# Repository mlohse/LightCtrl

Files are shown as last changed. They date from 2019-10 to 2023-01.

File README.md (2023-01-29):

# LightCtrl

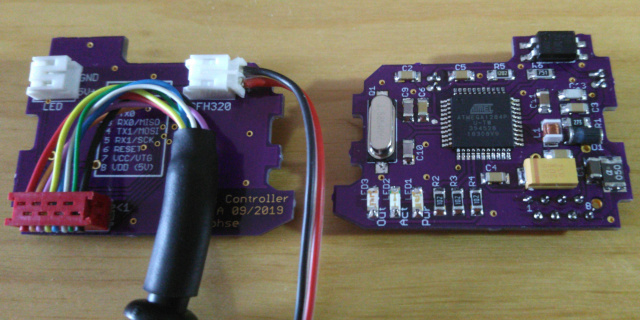
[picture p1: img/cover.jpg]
cover image


Light Controller for Egret TenV4 electric scooter

The goal of this project is to power the scooter's front light from the main LiPo battery instead of using 4x throw-away alkaline batteries (AAA).
Further, it allows the light to be switched on/off conveniently via the throttle controller's power button (same as the rear light)
or have the light switched on/off automatically when it's getting dark (e.g. in tunnels or at night).

The PCB needs to be installed into the front light's battery compartment. The on/off switch is no longer needed and can be replaced by a photo transistor.

A short demo video (German) is available on vimeo: https://vimeo.com/364582430

# Required Skills
Before you consider building your own, please be aware that you'll need some skills here:

* You should be able to solder SMD! I've chosen large components (1206) for the PCB, but of course there is the 44-pin package of the ATMEGA, which may need some practice and a decent solder iron/station.

* The PCB and front light is powered via the 5V USB supply of the scooters throttle controller and needs to be connected in series to the throttle controller's tx data line (white cable).
  This can be accomplished by either opening/modifying the throttle controller (see instructions below) or creating an adapter cable which can be installed between the throttle and the motor controller (in the battery compartment).

* The front light's plastic case needs some mechanical modification to fit a cable through the housing (drill a hole) and fit PCB into the battery compartment.

* You'll need to remove the front light's on/off switch and solder wire between the voltage regulators enable pin (again SMD) and ground, see description below...

* You'll need an ISP-programmer for flashing the firmware (those are available on Ebay for ~15 Euro)

This project is certainly not suitable for beginners and of course I won't take any liability if you break your scooter or any components of it.

# Bill of Material (BOM)
The PCB can be ordered at OSH Park (they ship worldwide):

* https://oshpark.com/shared_projects/gwnaN0r6 (rev.B)

It doesn't really matter of which brand/type you order resistors and capacitors, nor does this board require any tight tolerances. You can purchase whatever your local hardware dealer has on stock fitting the value/package described by the schematic.
However, for convenience I've created a virtual shopping basket at Reichelt Elektronik:

* https://www.reichelt.de/my/1627216

Unfortunately, the AQY212EH isn't available at Reichelt, but you can order it from Buerklin,
Order-No.: 29G8736

* https://www.buerklin.com/de/Produkte/Elektromechanik/Relais-und-Sch%C3%BCtze/PhotoMOS-Relais/AQY-212-EHA%2C-SMD-Relais/p/29G8736

Further, I've tried several (low-cost) usb cables from Amazon which didn't quite fit my needs, until I came across these 2:

* https://www.amazon.de/gp/product/B01I1HXRK8/ (this is actually much shorter than 40cm, I measured only 34cm!)

* https://www.amazon.de/gp/product/B00P0ES0VC/

The UGreen USB3 extension cable is of decent quality and can be crimped perfectly into the Micromatch connector.
(Yes, it needs to be cut into halves: The female connector is needed for the front light, the male can be used to build an adapter for the ISP programmer)

# Building and Flashing the Firmware
You need to have an AVR toolchain installed (make, gcc, binutils)

On Arch Linux simply install the following packages:

`# pacman -S community/avr-gcc community/avr-binutils community/avr-libc`

I'm still using my good old AVR Dragon (unfortunately, it seems to be out of production), which needs to have avrdude installed:

`# pacman -S avrdude`

If you own a different programmer there is a good chance it's also supported by avrdude, otherwise just install whatever software it needs and don't forget to adopt the programmer/fuses section of the Makefile accordingly.

To build the firmware change into the `src` directory and run:

`# make`

...then connect the board to your ISP programmer (it needs to be powered through the programmer!) and flash the fuses:

`# make fuses`

...and firmware:

`# make program`

Done.

# Front Light PCB Modification
1. Remove the on/off switch and undervoltage indicator led (no longer needed)
2. Connect the voltage regulator's enable pin (outer pin) to GND, as shown:
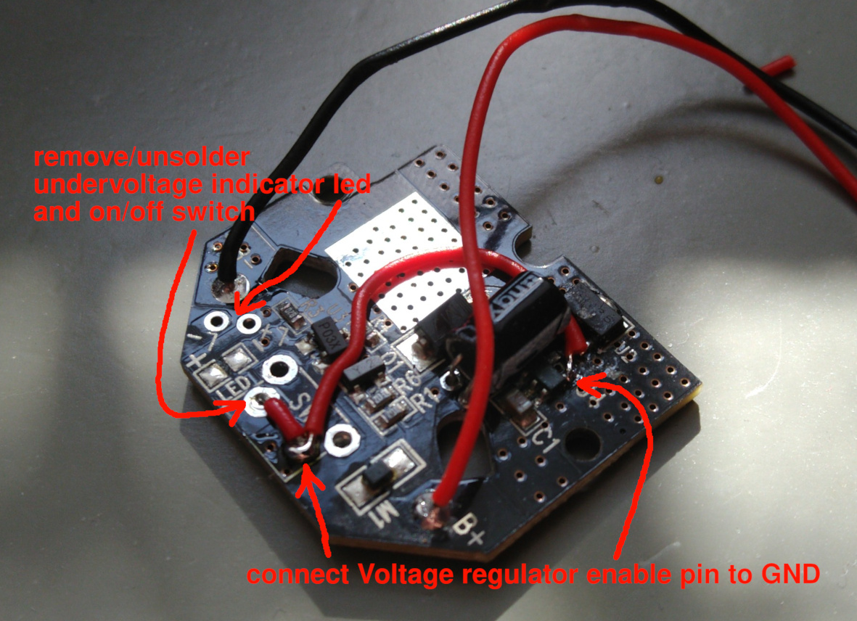
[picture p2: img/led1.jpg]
front light pcb modification


# Throttle Controller Modification
1. Open the throttle controller (it is glued with silicone and requieres some force - use a knife or sharp piece of metal). Once open remove the USB socket which is also glued in with silicone and clean it as best as you can:
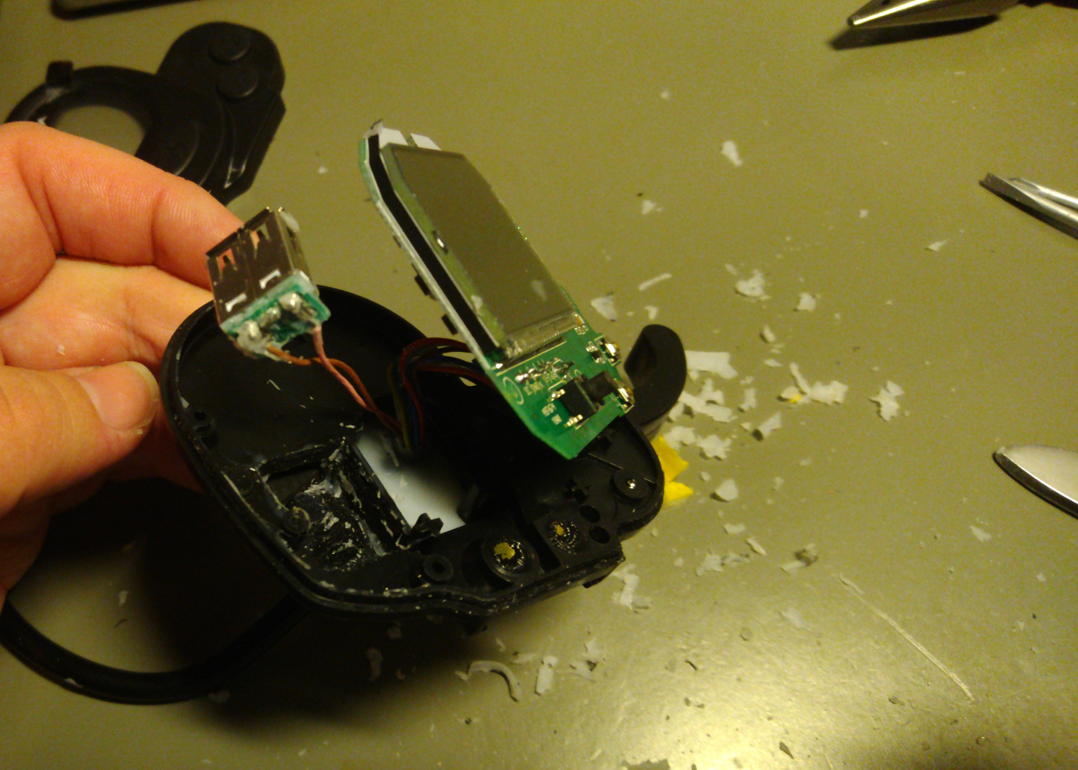
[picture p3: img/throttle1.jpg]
open throttle controller


2. Unsolder the TX data wire (white, labels as T6):
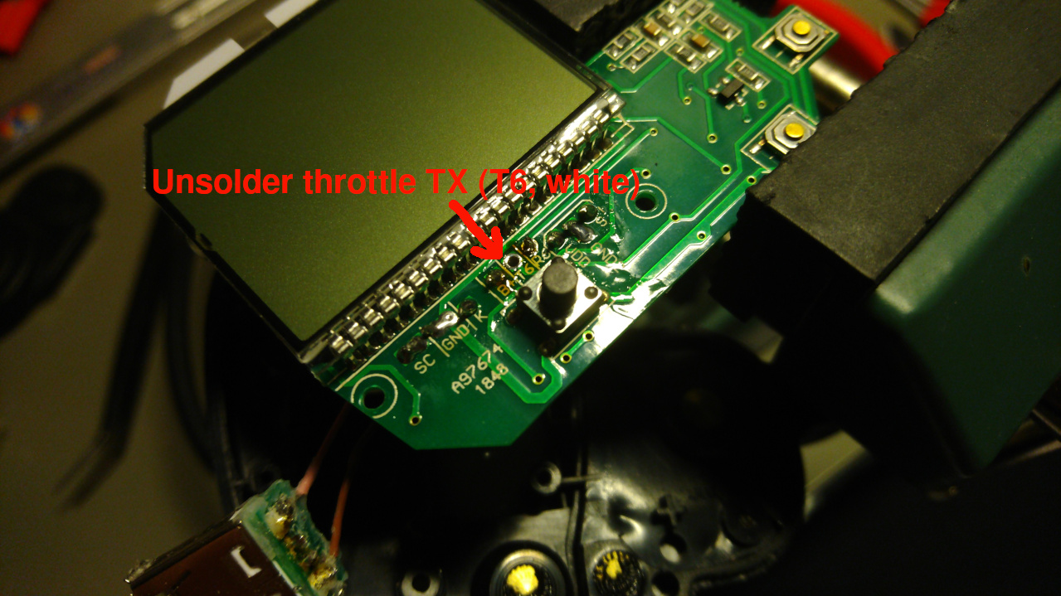
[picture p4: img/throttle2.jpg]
tx data wire


3. Open the solder bridge between the USB data lines:
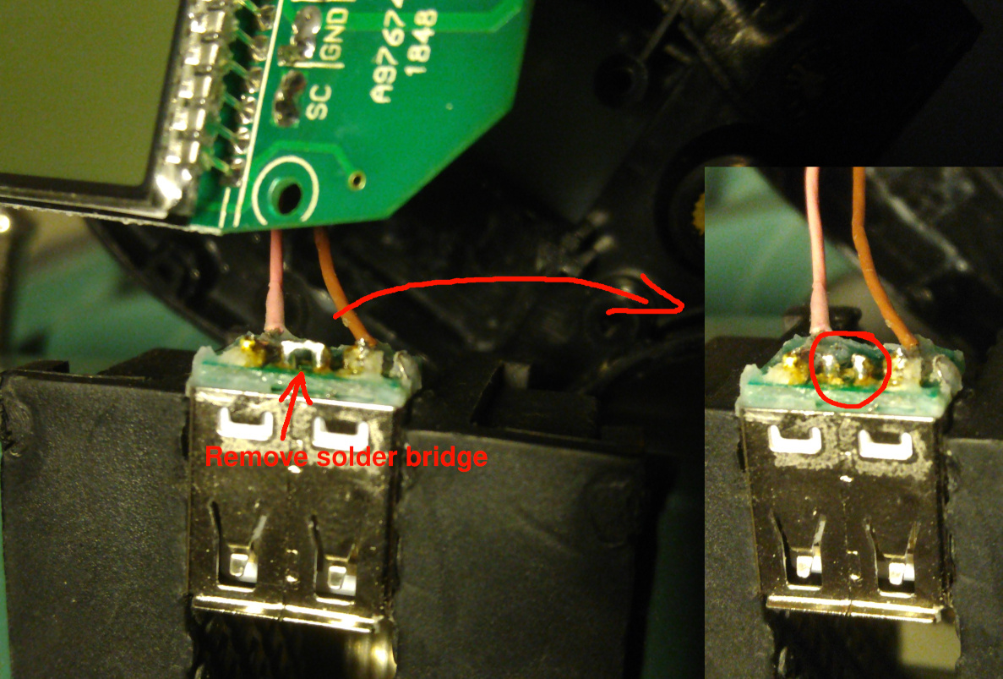
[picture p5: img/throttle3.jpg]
usb solder bridge


4. Conntect the white cabel (which was soldered to throttle T6 previously) to the USB data line and add a new cable from the other usb data line to the throttle's T6 pin. Note: the 4k7 resistor is optional. If it is installed the scooter can be started without the LightCtrl pcb connected. If it is not fitted, the throttle will show an error if powered on without it. This may be usefull as a weak theft-protection (if you take the front-light with you when you leave the scooter alone).
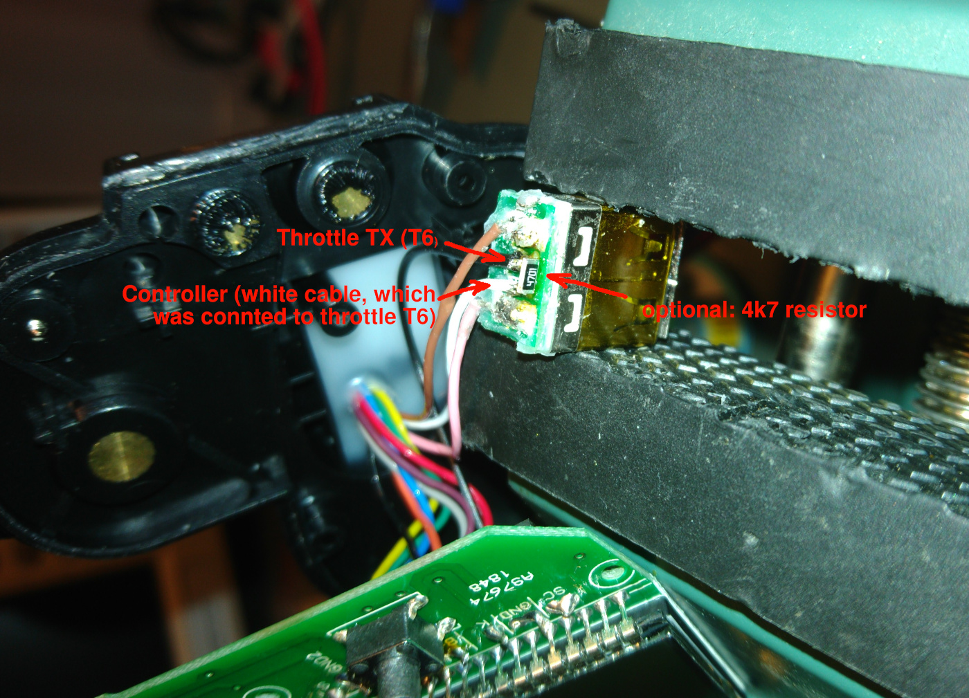
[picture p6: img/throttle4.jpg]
usb data lines connected


5. Use some hot glue to put the USB socket back in
Important: After modification the USB socket can no longer be used to charge usb devices! Do not plug in your cell phone!

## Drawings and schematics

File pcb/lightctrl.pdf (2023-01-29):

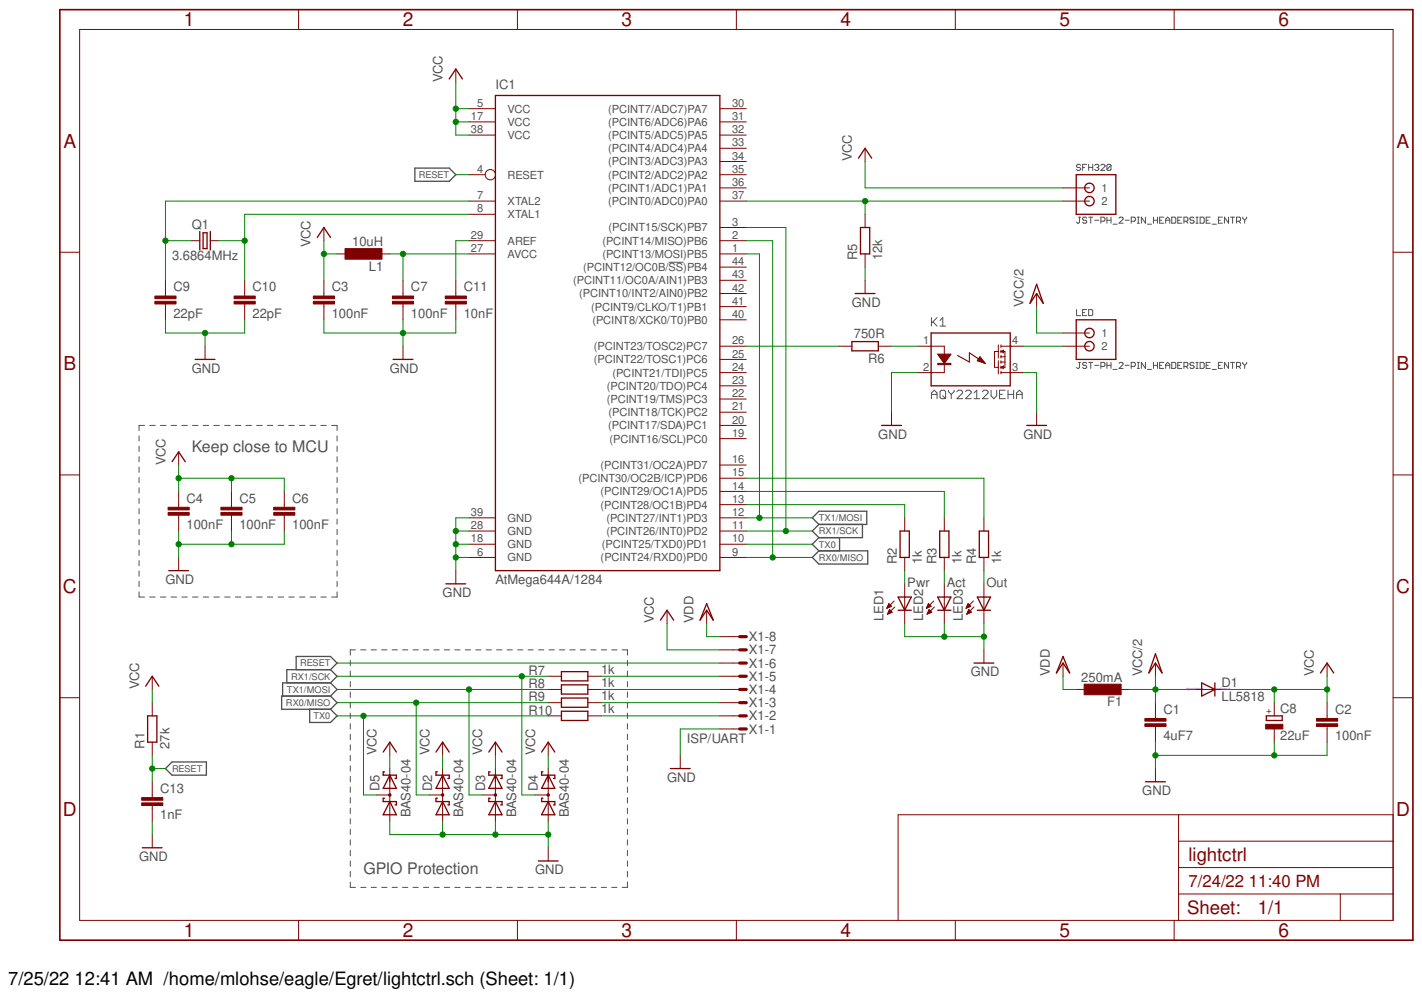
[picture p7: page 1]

VCC
Keep close to MCU

7/25/22 12:41 AM /home/mlohse/eagle/Egret/lightctrl.sch (Sheet: 1/1)

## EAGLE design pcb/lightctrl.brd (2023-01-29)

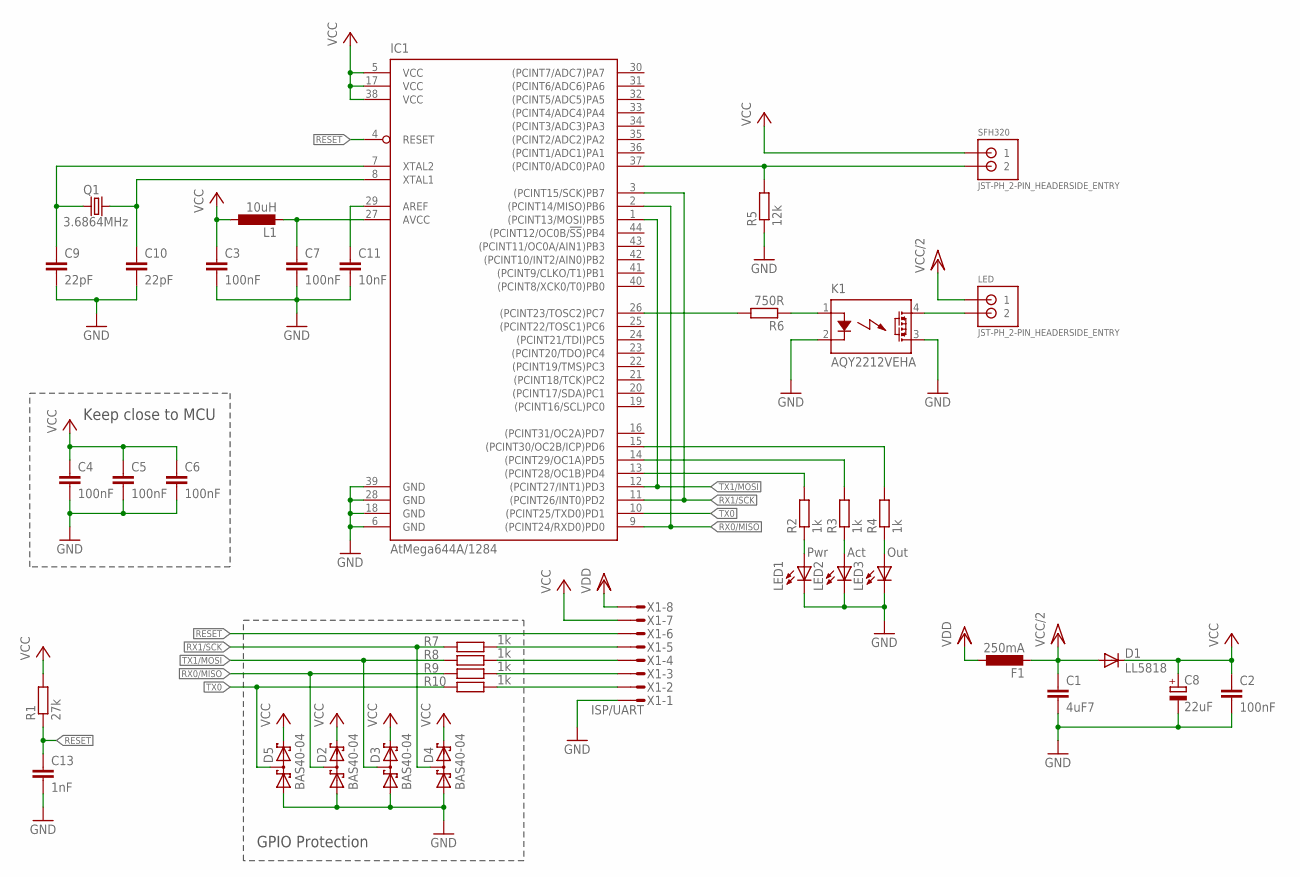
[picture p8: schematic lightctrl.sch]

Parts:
C1: 4uF7; C1206
C2, C3, C4, C5, C6, C7: 100nF; C1206
C8: 22uF; SMC_D
C9, C10: 22pF; C1206
C11: 10nF; C1206
C13: 1nF; C1206
D1: LL5818; MELF-MLL41
D2, D3, D4, D5: BAS40-04; SOT23
F1: 250mA; L1812
IC1: AtMega644A/1284; TQFP44
K1: AQY2212VEHA; SMD-DIP04
L1: 10uH; L3230M
LED: JST-PH_2-PIN_HEADERSIDE_ENTRY; S2B-PH_HEADER
LED1: Pwr; CHIPLED_1206
LED2: Act; CHIPLED_1206
LED3: Out; CHIPLED_1206
Q1: 3.6864MHz; HC49UP
R1: 27k; R1206
R2, R3, R4, R7, R8, R9, R10: 1k; R1206
R5: 12k; R1206
R6: 750R; R1206
SFH320: JST-PH_2-PIN_HEADERSIDE_ENTRY; S2B-PH_HEADER
X1: ISP/UART; MICROMATCH-8

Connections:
GND: C1.2, C2.2, C3.2, C4.2, C5.2, C6.2, C7.2, C8.-, C9.2, C10.2, C11.2, C13.2, D2.1 (A1), D3.1 (A1), D4.1 (A1), D5.1 (A1), IC1.6 (GND), IC1.18 (GND), IC1.28 (GND), IC1.39 (GND), K1.2 (K), K1.3 (DS2), LED1.C, LED2.C, LED3.C, R5.1, X1.1
unnamed: C7.1, IC1.27 (AVCC), L1.2
unnamed: IC1.37 ((PCINT0/ADC0)PA0), R5.2, SFH320.P2 (2)
unnamed: C11.1, IC1.29 (AREF)
unnamed: C10.1, IC1.8 (XTAL1), Q1.2
unnamed: C9.1, IC1.7 (XTAL2), Q1.1
unnamed: K1.4 (DS1), LED.P2 (2)
unnamed: LED1.A, R2.1
unnamed: LED2.A, R3.1
unnamed: LED3.A, R4.1
unnamed: IC1.13 ((PCINT28/OC1B)PD4), R2.2
unnamed: IC1.14 ((PCINT29/OC1A)PD5), R3.2
unnamed: IC1.15 ((PCINT30/OC2B/ICP)PD6), R4.2
unnamed: R7.2, X1.5
unnamed: K1.1 (A), R6.1
unnamed: R8.2, X1.4
unnamed: R9.2, X1.3
unnamed: IC1.26 ((PCINT23/TOSC2)PC7), R6.2
unnamed: R10.2, X1.2
RESET: C13.1, IC1.4 (RESET), R1.1, X1.6
RX0/MISO: D2.3 (C1A2), IC1.2 ((PCINT14/MISO)PB6), IC1.9 ((PCINT24/RXD0)PD0), R9.1
RX1/SCK: D4.3 (C1A2), IC1.3 ((PCINT15/SCK)PB7), IC1.11 ((PCINT26/INT0)PD2), R7.1
TX0: D5.3 (C1A2), IC1.10 ((PCINT25/TXD0)PD1), R10.1
TX1/MOSI: D3.3 (C1A2), IC1.1 ((PCINT13/MOSI)PB5), IC1.12 ((PCINT27/INT1)PD3), R8.1
VCC: C2.1, C3.1, C4.1, C5.1, C6.1, C8.+, D1.C, D2.2 (C2), D3.2 (C2), D4.2 (C2), D5.2 (C2), IC1.5 (VCC), IC1.17 (VCC), IC1.38 (VCC), L1.1, R1.2, SFH320.P1 (1), X1.7
VCC/2: C1.1, D1.A, F1.2, LED.P1 (1)
VDD: F1.1, X1.8

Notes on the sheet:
GPIO Protection
Keep close to MCU

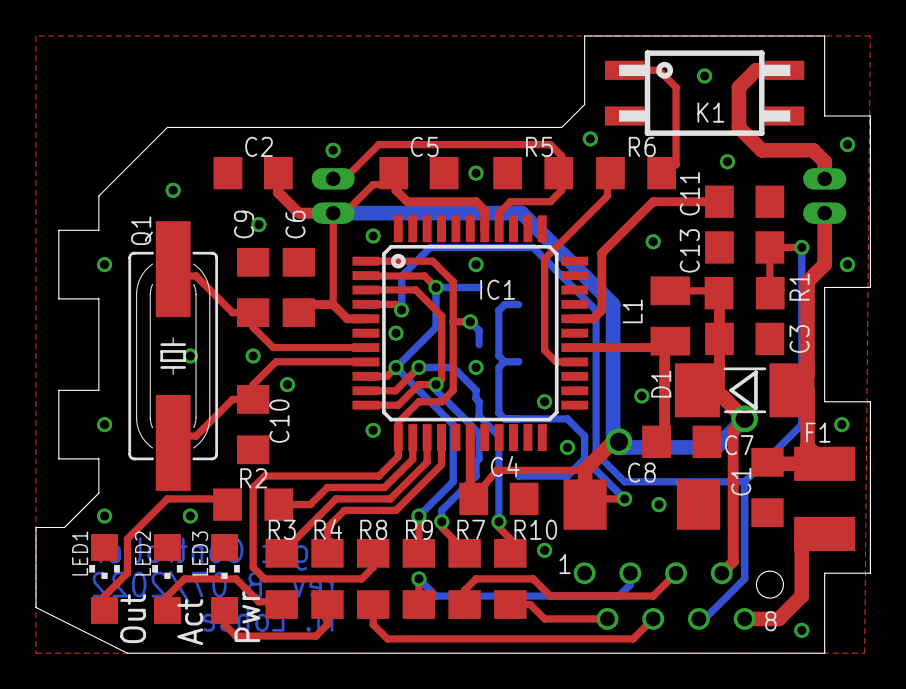
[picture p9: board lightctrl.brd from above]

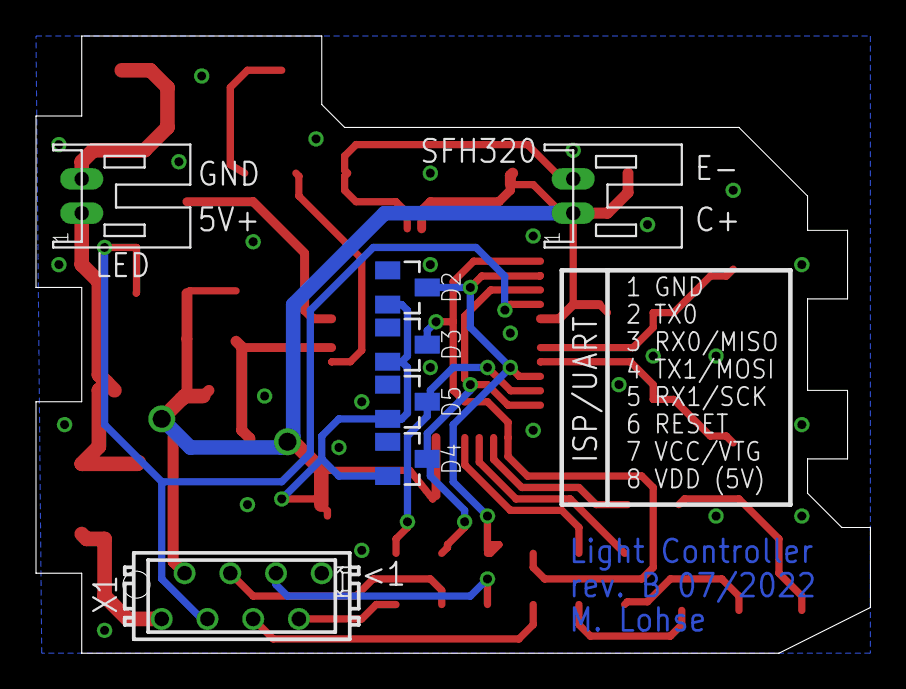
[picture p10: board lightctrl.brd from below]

Board: 2 copper layers, 46.4 x 34.3 mm, 38 parts (7 on the bottom side), 27 nets.

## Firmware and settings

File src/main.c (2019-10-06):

/*******************************************************************************
 * main.c                                                                      *
 * author:  Markus Lohse <mlohse@gmx.net>                                      *
 * date:    2019-09-24                                                         *
 * license: LGPLv3, see https://www.gnu.org/licenses/lgpl-3.0.txt              *
 ******************************************************************************/
#include <avr/io.h>
#include "adc.h"
#include "led.h"
#include "uart.h"
#include "config.h"
#include "ctrl.h"
#include "timer.h"


static void init(void)
{
	/* configure & initialize io ports */
	DDRA = IO_DDRA;
	DDRB = IO_DDRB;
	DDRC = IO_DDRC;
	DDRD = IO_DDRD;
	
	PORTA = INIT_PORTA;
	PORTB = INIT_PORTB;
	PORTC = INIT_PORTC;
	PORTD = INIT_PORTD;

	timer_init();
	uart_init();
	led_flash();
	uart0_flush();
	adc_init();
}

int main(void)
{
	init();
	adc_start();

	while(1)
	{
		ctrl_run();
		led_set(LED_PWR, (timer_uptime() % 2000) < 1000);
	}
}

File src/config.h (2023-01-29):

/*******************************************************************************
 * Config file for Egret Light Controller board rev. A                         *
 * author:  Markus Lohse <mlohse@gmx.net>                                      *
 * date:    2019-09-24                                                         *
 * license: LGPLv3, see https://www.gnu.org/licenses/lgpl-3.0.txt              *
 ******************************************************************************/
#ifndef CONFIG_H_
#define CONFIG_H_

/***********************************
 * IO Ports                        *
 ***********************************/
#define IO_DDRA                 0xFE    // PortA [1..7] unused out, 0 sensor input
#define IO_DDRB                 0x1F    // PortB [0..4] unused out, 5 mosi/tx1 -> PD3 in, 6 miso/rx0 -> PD0 in, 7 sck/rx1 -> PD2 in
#define IO_DDRC                 0xFF    // PortC [0..6] unused out 7 switch out
#define IO_DDRD                 0x8C    // PortD [0,1] UART0 in, [2,3] UART1 unused out, [4..6] LED1-3 out, 7 unused out

/* led definition for led.h */
#define PORT_LED0               PORTC
#define PORT_LED1               PORTD
#define PORT_LED2               PORTD
#define PORT_LED3               PORTD
#define PIN_LED0                7       // light switch, simply treat it as led
#define PIN_LED1                4       // Pwr - blue
#define PIN_LED2                5       // Act - green
#define PIN_LED3                6       // Out - red

#define LED_NUM                 4

/* to be used with led_on, led_off,... */
#define LED_LIGHT               0
#define LED_PWR                 1
#define LED_ACT                 2
#define LED_OUT                 3


/***********************************
 * Initialization                  *
 ***********************************/
#define INIT_PORTA              0x00    // pull unused pins to GND, disable pullup on PortA,0 (light sensor)
#define INIT_PORTB              0x00    // pull unused pins to GND, disable pullups for mosi/miso/sck
#define INIT_PORTC              0x00    // pull unused pins to GND, switch off led light
#define INIT_PORTD              0x00    // pull unused pins to GND, switch off leds, disable pullup on UART(s)


/***********************************
 * UART Settings                   *
 ***********************************/
#define BUFFER_SIZE_TX0         32      // in bytes, must be between 1 and 255, should be at least (UART_MSG_SIZE_MAX * 2) + 2
#define BUFFER_SIZE_TX1         1
#define BUFFER_SIZE_RX0         32
#define BUFFER_SIZE_RX1         36
#define UART0_ENABLE                    // undefine to disable uart interface(s)
//#define UART1_ENABLE

/* baud rate */
#define UART0_UBRR              0x005F  // @3.6864MHz -> 2400Baud
#define UART1_UBRR              0x0077


/***********************************
 * Throttle/Display Controller     *
 ***********************************/
#define THROTTLE_VERSION        0       // V4 = 0 or V3X = 1 (see msg.h)


/***********************************
 * Light sensor                    *
 ***********************************/
#define LIGHT_SENS_PORT         PORTA
#define LIGHT_SENS_PIN          0       // PortA,0
#define LIGHT_SENS_THRES_OFF    150     // ADC threshold for switching light off
#define LIGHT_SEND_THRES_ON     60      // ADC threshold for switching light on
//#define LIGHT_AUTO_INTERVAL_MAX 10000   // autolight toggle max. interval in msec


/***********************************
 * Sleep Mode                      *
 ***********************************/
#define SLEEP_BOD_DISABLE               // uncomment to disable brown out detect during sleep (reduces pwr consumption)
#define SLEEP_WAKEUP_PCINT      14      // wakeup on pin change irq PB6 (rx0/mosi)
#define SLEEP_ACT_TIMEOUT       1750    // fall asleep after not receiving any uart message for x milliseconds

#endif /* CONFIG_H_ */

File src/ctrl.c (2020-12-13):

/*******************************************************************************
 * Light controller application                                                *
 * author:  Markus Lohse <mlohse@gmx.net>                                      *
 * date:    2019-09-24                                                         *
 * license: LGPLv3, see https://www.gnu.org/licenses/lgpl-3.0.txt              *
 ******************************************************************************/
#include <stdint.h>
#include "config.h"
#include "ctrl.h"
#include "msg.h"
#include "led.h"
#include "adc.h"
#include "uart.h"
#include "sleep.h"


static uint8_t ctrl_autolight(void)
{
	static uint8_t lighton = 0;
	uint16_t val = adc_read();
	if (val < LIGHT_SEND_THRES_ON)
	{
		lighton = 1;
	}
	if (val > LIGHT_SENS_THRES_OFF)
	{
		lighton = 0;
	}
	return lighton;
}

void ctrl_run(void)
{
	throttle_msg_t *msg;
	static uint8_t autolight = 1;

	if (uart0_bytes_available())
	{
		led_on(LED_ACT);
	}

	msg = msg_parse();
	if (msg)
	{
		uint8_t light = (msg->flags & FLAG_LIGHT_ENABLED) ? 1 : 0;
		switch(msg->mode)
		{
			case THROTTLE_MODE0:
				if (!light) /* (re-)enable autolight by switching to Mode0 */
				{
					autolight = 1;
				}
				break;
			default: /* THROTTLE_MODE1..5 */
				if (light) /* disable autolight if user switches it on manually */
				{
					autolight = 0;
				}
				break;
		}
		if (autolight)
		{
			light = ctrl_autolight(); /* overwrite light setting of throttle */
		}
		msg->flags = light ? (msg->flags | FLAG_LIGHT_ENABLED) : (msg->flags & ~FLAG_LIGHT_ENABLED);
		msg_send(msg); /* forward (modified) message to control unit */

		led_set(LED_OUT, light);
		led_set(LED_LIGHT, light); /* set front light */
		led_off(LED_ACT);
	}
	if (sleep_ready())
	{
		ctrl_sleep();
		autolight = 1; /* enable autolight when scooter is switch on */
	}
}

void ctrl_sleep(void)
{
	adc_stop();
	led_off(LED_ACT);
	led_off(LED_PWR);
	led_off(LED_OUT);
	led_off(LED_LIGHT);
	sleep_powerdown();
	adc_start();
}

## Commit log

2019-10-03 initial version
    [lightctrl.brd, lightctrl.sch]
2019-10-03 add project description and BOM
2020-12-14 add instructions for modifying throttle controller and front light's pcb
2023-01-29 Update pcb and documentation to rev.B: fix padsize for D1, add gpio protection for MCU, slightly widen board to get better grip in battery compartment
    [lightctrl.brd, lightctrl.sch]
